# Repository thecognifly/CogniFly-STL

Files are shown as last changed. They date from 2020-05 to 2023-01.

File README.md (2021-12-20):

# CogniFly-STL
3D files (STL) for printing and assembling current and past versions of CogniFly

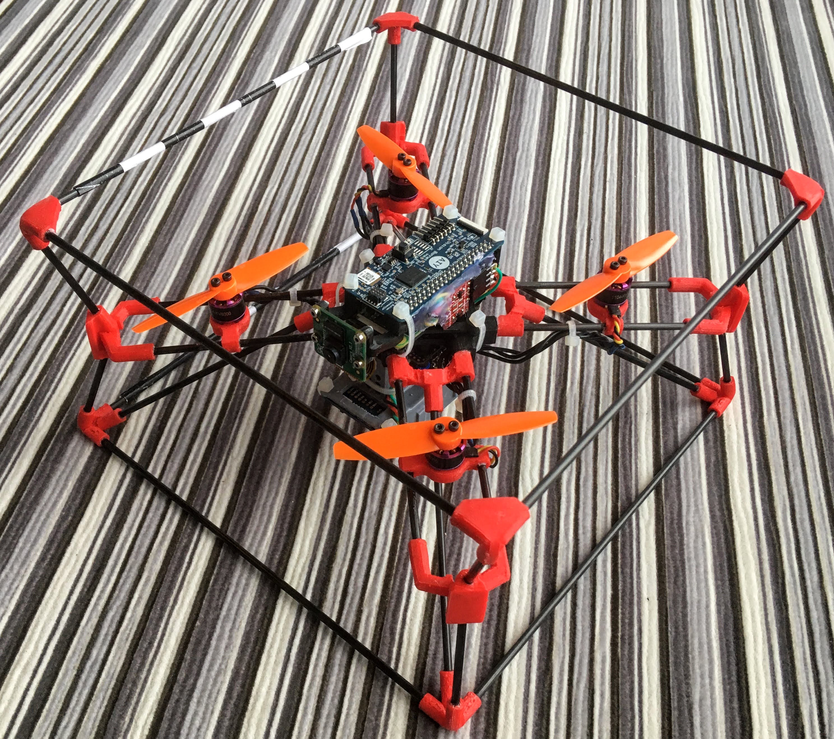
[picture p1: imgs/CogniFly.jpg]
CogniFly


Fold as you assemble

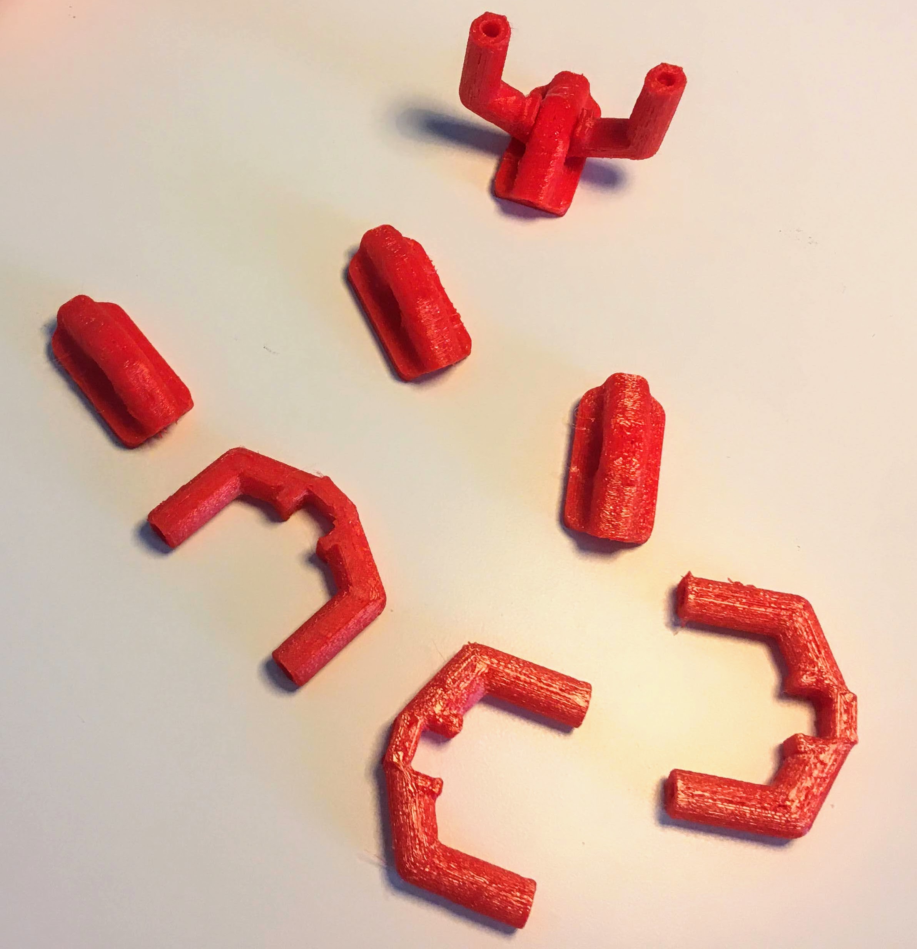
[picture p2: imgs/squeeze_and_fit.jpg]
Squeeze and fit


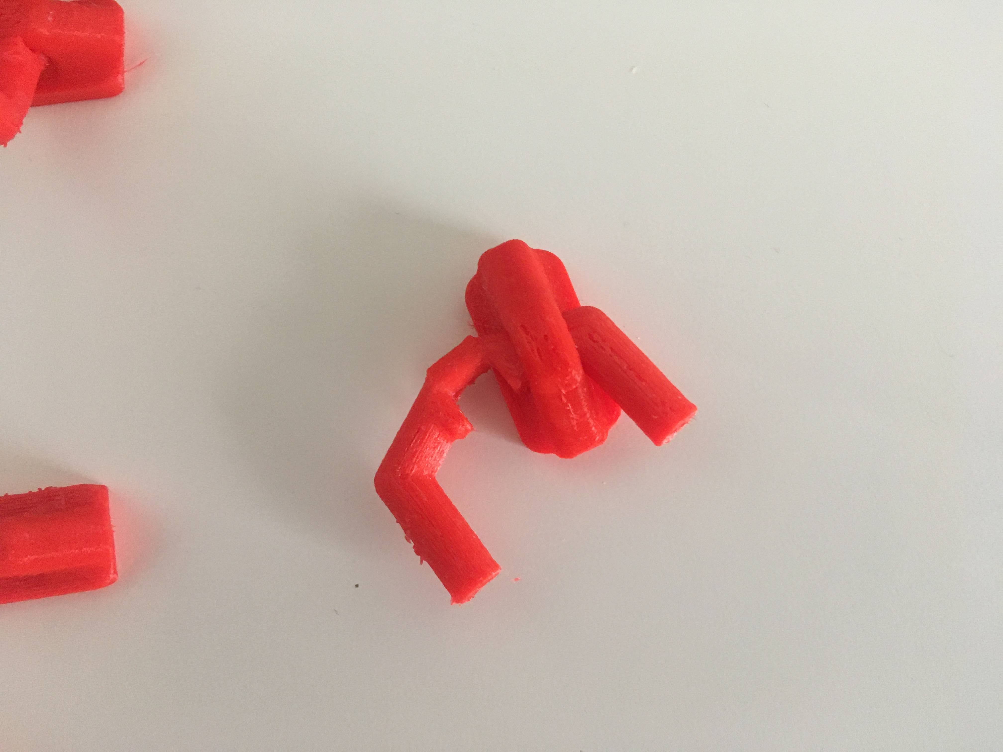
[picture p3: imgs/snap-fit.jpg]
Squeeze and fit 2

It's a very snug fit! You need to squeeze the round tube-like side, but without damaging it. Probably the hardest part to assemble.

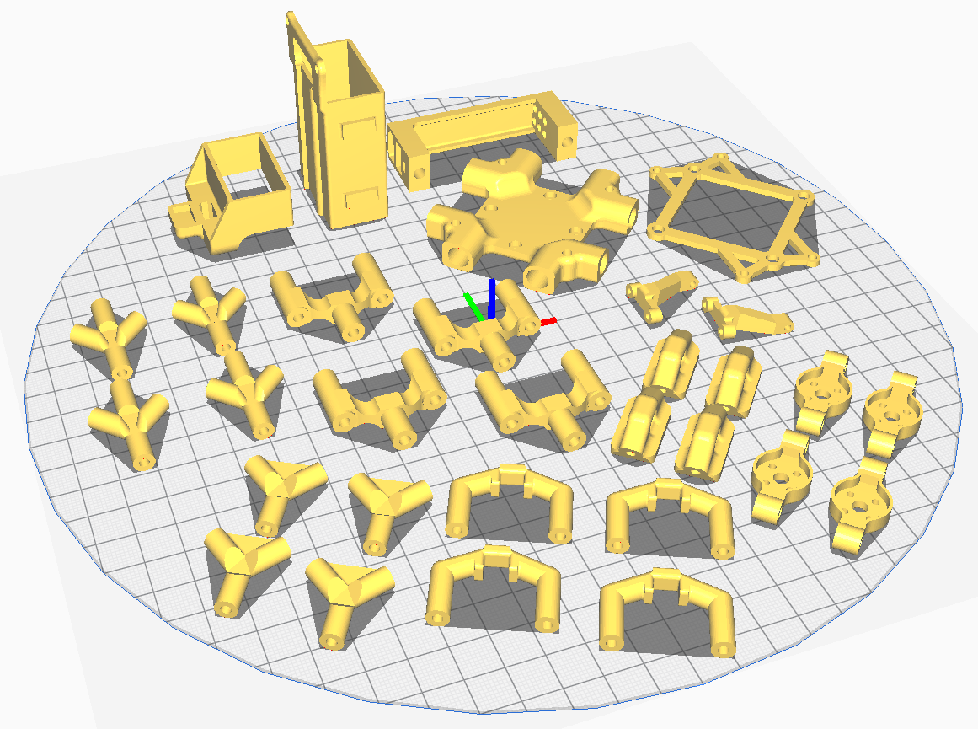
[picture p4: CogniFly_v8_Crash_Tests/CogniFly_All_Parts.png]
All parts together as they should be printed

The only part that needs support to be printed is the [Battery_holder_magnetic_lid.stl](CogniFly_v8_Crash_Tests/Battery_holder_magnetic_lid.stl). Depending on your printer, settings, fillament, etc. some holes will change the internal diameter and they may be too loose. In this case, you will need to glue the struts (carbon fiber or bamboo skewers) or, instead of absorbing the impact, the frame will just fall apart and almost no impact energy will be absorbed by the flexible parts. If you get a nice snug-fit between the struts and the TPU parts, you will not need to glue them together. In the case of bamboo, because they break much more easily than carbon fiber (never managed to break any!), if you glue them it will be annoying to replace.

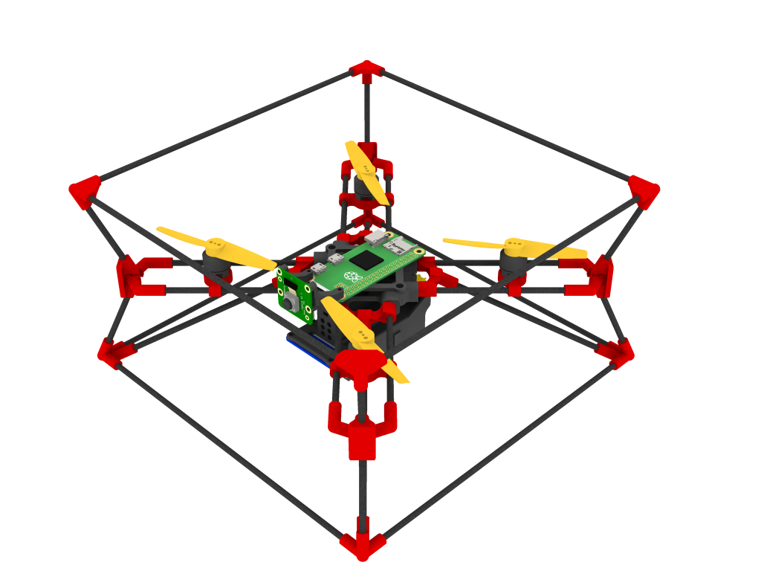
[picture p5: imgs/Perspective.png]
Render

All the parts in red are made of flexible TPU 95A. 

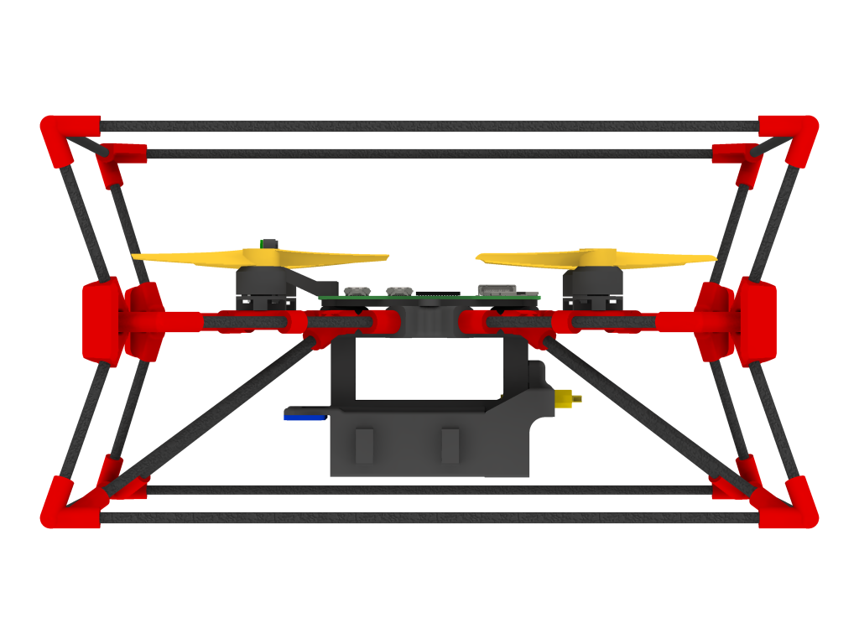
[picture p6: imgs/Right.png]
FC and ESC

Flight controller and ESC (4-in-1) are mounted between the battery and the central part of the frame (the empty space seeing above). The central was designed with 20x20mm mounting holes. The motors shown in the photograph at the top are 1104 ones and the holes are for M2, but be careful with the length of your screws so you don't destroy the motor windings!

## Bill of Materials (BOM)
### Brushless Motors and Propellers
- (4x) 1104 6000KV (use with 3025 2 blades propeller, used in our paper)  
**or**   
- (4x) 1106 3800KV (use with 4025 2 blades propeller, and it will need a bigger frame / longer struts or the [experimental motor bases](https://github.com/thecognifly/CogniFly-STL/blob/master/CogniFly_v8_Crash_Tests/MotorBase_Shorter_Taller.stl) to avoid hitting the RPI or AIY Bonnet)
### 3D Printing Filament
- TPU 95A for flexible parts
- PLA or ABS for the rigid ones
### Struts
- 3mm diam. carbon fibre rods or BBQ bamboo skewers with these approximate lengths: 8x 195mm (*"external cage"*), 8x 97mm (arms) and 4x 72mm (legs).
### Flight Controller (20x20mm mounting holes)
- (1x) Holybro Kakute F7 Mini V2 (used in our paper) or Heli-Nation Talon F7 Fusion
### 4 in 1 ESC (20x20mm mounting holes)
- (1x) Anyone that can deliver around 15A or 20A per motor to be safe (Spedix IS35 35A used in our paper)
### Firmware
- [Our INav fork with targets: KAKUTEF7 or CLRACINGF7](https://github.com/thecognifly/inav/tree/CogniFly)
- The standard INav should also work, but you will need to check if your flight controller is supported. BetaFlight will work, but it doesn't offer position hold.
### Battery
- LiPo Battery 650mAh 11.1V 75C 3S (TATTU used in our paper)
### Single-Board Computer
- [Raspberry Pi Zero W](https://www.raspberrypi.org/products/raspberry-pi-zero-w/)
### Camera
- [Raspberry Camera V2](https://www.raspberrypi.org/products/camera-module-v2/)
### Optical Flow and Time-of-Flight sensor
- [Matek Optical Flow and Lidar sensor](http://www.mateksys.com/?portfolio=3901-l0x)
### Neural Network Accelerator
- [Google AIY Vision Kit](https://aiyprojects.withgoogle.com/vision) (the Raspberry Pi Zero W + Camera are included). You don't really need it unless you want to run some neural network models. You can try the [Google Coral Edge TPU USB](https://github.com/ricardodeazambuja/libedgetpu-rpi0/releases/tag/rpi0_tflite_edgetpu) with [an adapter](https://shop.pimoroni.com/products/usb-to-microusb-otg-converter-shim) as well.
### Extras
- (1x) XT30 connector + cable to solder it to the ESC
- Cable zip ties (approx. 2mm wide)
- M2 screws / nuts / rubber rings to mount the ESC and FC (they usually come with the FC).
- Screws for mounting the motors and propellers (check the motor's manual to avoid damaging the motor with screws that are too long!)

## Caveats
1. The connection between one of the RPI Zero UARTs ([it has two](https://www.raspberrypi.org/documentation/configuration/uart.md)) and the flight controller may suffer from external interference, so twist it, try to use the shortest length, and keep it away from other cables (specially high current ones). For the same reason, some of the unused [pins from the AIY Vision Bonnet](https://pinout.xyz/pinout/aiy_vision_bonnet) were trimmed down to avoid problems with interference.
2. If you use super glue to assemble the bamboo version, it will be very hard to remove the bamboo sticks from the flexible 3D printed parts if the bamboo breaks.
3. The way parts are placed on the 3D printer bed is very important when using FDM printers because they will dramatically change the way the part behaves (weaker in some directions, layer adhesion, etc). Therefore, try to follow the suggested directions.
4. Carbon fiber needs to be cut using water / wet tissue to avoid problems with the fine dust generated, but even like that it's a serious health hazard. If you are not sure, start with the bamboo version. **Don't forget to wear protective equipment!**
5. We suggest initially building the frame using BBQ bamboo skewers (no glue!) so you will have the perfect template for cutting the carbon fibre rods later. The frame can be made bigger or smaller up to a certain scale just by choosing the correct lengths for the struts.

## Finally, this is a collision *resilient* design, but it has its physical limits as everything else in life. It will absorb a lot of energy even in the case where it flex so much that you manage to hit the internal electronics agains the obstacle, but in this case it may damage something that is fragile. We used poly carbonate propellers and they lasted quite a few crashes before becoming too damaged for flying :)

**For more details, check [thecognifly.github.io](https://thecognifly.github.io/).**

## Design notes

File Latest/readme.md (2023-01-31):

# Building Instructions (Version 2)

The Cognifly is a sub-250g drone with easy manufacturing, allowing
customization and autonomous flight. It has an optical flow and lidar,
allowing position and altitude hold, and a Raspberry Pi Zero W, allowing
wireless control and data processing. A Pi camera linked to the
Raspberry pi allows image processing to do an autonomous flight. The
flight controller is working with INAV, which allows an easy
configuration of the drone.

The frame is built with wood sticks and resists to impact while flying.
Another configuration is possible with carbon fiber, but it is more
expensive and heavier. The bamboo version of CogniFly weighs 237g (and, depending on the materials used, from 246 to 255g if you swap bamboo for carbon fibre rods in THIS version). It uses a LiPo battery 2S (7,4V) with a
2000mAh capacity, leading to a 17-minute flight time. (The test has been
made in one long flight, from 8,4V to 6,6V, in the position hold mode).

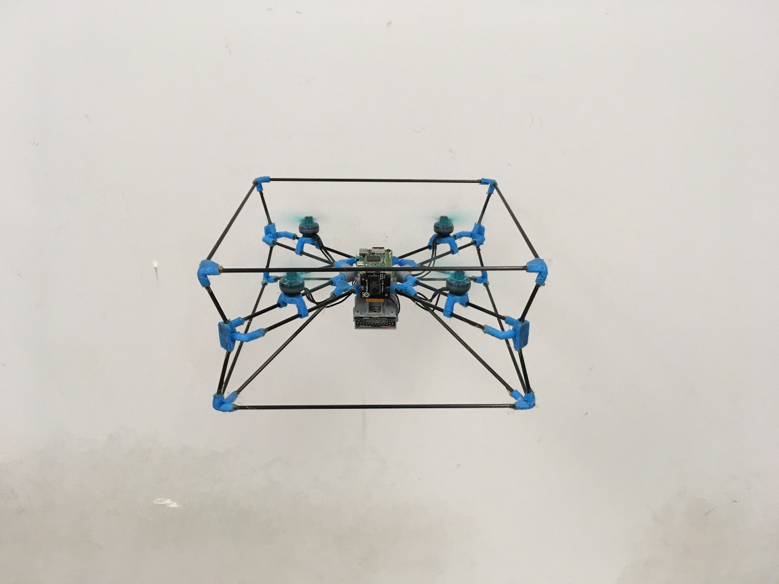
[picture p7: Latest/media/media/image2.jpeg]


## Table of Contents
1. [Bill of Materials](readme.md#bill-of-materials)
    * [Table 1: Description of the hardware for one drone](readme.md#table-1-description-of-the-hardware-for-one-drone)
    * [Table 2: Bill of Materials using a Raspberry Pi Zero](readme.md#table-2-bill-of-materials-using-a-raspberry-pi-zero)
    * [Table 3: Bill of Materials using a Google AIY Vision Kit](readme.md#table-3-bill-of-materials-using-a-google-aiy-vision-kit)
    * [Table 4: Bill of Materials using a Coral board](readme.md#table-4-bill-of-materials-using-a-coral-board)
2. [Building the drone](readme.md#building-the-drone)
    * [Frame](readme.md#frame)
    * [Electronics](readme.md#electronics)
    * [Putting everything together](readme.md#putting-everything-together)
3. [Software setup](readme.md#software-setup)
    * [INAV](readme.md#inav)
    * [Raspberry Pi Zero W](readme.md#raspberry-pi-zero-w)
4. [Troubleshooting](readme.md#troubleshooting)
    * [Wifi not working](readme.md#wifi-not-working)
    * [ssh not available](readme.md#ssh-not-available)
    * [Flashing the FC](readme.md#flashing-the-fc)
5. [Acknowledgements](readme.md#acknowledgements)

## Bill of Materials

To build this drone, some tools will be needed and not included in the
following list: a 3D printer (ideally two so you can print continuously
the TPU parts and the PLA parts for more than 1 drone), a soldering iron
with tin (and flux), a hot glue gun with glue, and a screwdriver for M2
screws, wire strippers, pliers…

### *Table 1: Description of the hardware for one drone*

<table>
<thead>
<tr class="header">
<th>Part Number</th>
<th>Item</th>
<th>Description</th>
<th>Quantity</th>
</tr>
</thead>
<tbody>
<tr class="odd">
<td>CF01-CF04</td>
<td><p>Wood stick</p>
<p><em>Or carbon fibre rods</em></p></td>
<td><p>Frame</p>
<p>Diameter: 3mm; Length : &gt;25cm</p></td>
<td>20 sticks</td>
</tr>
<tr class="even">
<td>CF05-CF10</td>
<td>TPU95a filament</td>
<td><p>Frame (Joints)</p>
<p>TPU95a filament; flexible plastic parts</p></td>
<td>34g</td>
</tr>
<tr class="odd">
<td>CF11-CF17</td>
<td>PLA filament</td>
<td><p>Structure</p>
<p>PLA filament; Hard plastic parts</p></td>
<td>24g</td>
</tr>
<tr class="even">
<td><p>CF18A</p>
<p>CF18B</p></td>
<td>Motor XING2 1404 3000KV</td>
<td><p>Motor XING2 1404<br />
3000KV; 10,1g</p>
<p>(7mm screws included used for propellers, Raspberry Pi, Camera, and optical flow attachment)</p></td>
<td><p>4</p>
<p>(18)</p></td>
</tr>
<tr class="odd">
<td>CF19</td>
<td>Screw spacer</td>
<td>M2/M3 Rubber Damping Ball (for raspberry pi and Optical flow)</td>
<td>4</td>
</tr>
<tr class="even">
<td><p>CF20A</p>
<p>CF20B</p></td>
<td>FC – ESC JHEMCU GHF420 35A</td>
<td><p>20x20mm Jhemcu GHF420AIO F4 OSD Flight Controller w/ 5V 9V BEC Output &amp; Built-in 35A BL_S 4In1 Brushless ESC</p>
<p>(4 Rubber Damping Balls included used for FC attachment)</p></td>
<td><p>1</p>
<p>(4)</p></td>
</tr>
<tr class="odd">
<td>CF21-CF22</td>
<td>Propellers 4024</td>
<td>Gemfan Hurricane 4024 2 Blades</td>
<td>2CW and 2CCW</td>
</tr>
<tr class="even">
<td>CF23</td>
<td>Matek Optical Flow and Lidar</td>
<td>Matek Optical Flow &amp; Lidar Sensor - 3901-L0X</td>
<td>1</td>
</tr>
<tr class="odd">
<td>CF24</td>
<td>Raspberry Pi Zero W</td>
<td>Raspberry Pi Zero W (Wireless)</td>
<td>1</td>
</tr>
<tr class="even">
<td>CF25</td>
<td>Pi camera</td>
<td>Raspberry Pi Camera V2 - 8MP</td>
<td>1</td>
</tr>
<tr class="odd">
<td>CF26</td>
<td>Mini camera cable</td>
<td>Raspberry Pi Zero Mini Camera Cable - 38mm</td>
<td>1</td>
</tr>
<tr class="even">
<td>CF27</td>
<td>Deans connector</td>
<td>Male Deans connector</td>
<td>1</td>
</tr>
<tr class="odd">
<td>CF28</td>
<td>SD card</td>
<td>Micro SD card &gt; 16Go</td>
<td>1</td>
</tr>
<tr class="even">
<td>CF29</td>
<td>Lipo 2S 2000mAh</td>
<td>Hosim Battery 9125; 2000 mAh LiPo Battery; 7,4V 25C</td>
<td>1 or more</td>
</tr>
<tr class="odd">
<td>CF30</td>
<td>M2 Screw 4mm</td>
<td>M2 Screw 4mm</td>
<td>16</td>
</tr>
<tr class="even">
<td>CF31</td>
<td>M2 Screw 16mm</td>
<td>M2 Screw 16mm</td>
<td>6</td>
</tr>
<tr class="odd">
<td>CF32</td>
<td>Wire 28/32 AWG</td>
<td>4 Wires 28/32 AWG (4 colors)</td>
<td>2X15cm</td>
</tr>
<tr class="even">
<td><em>CF33</em></td>
<td>Vision Bonnet</td>
<td>Google AIY Vision Bonnet</td>
<td>1 (<em>optional</em>)</td>
</tr>
</tbody>
</table>

The Vision bonnet is optional but allows to compute more data faster,
which can be useful for image processing.

The following tables (2 to 4) presents some website where to order the
material. Table 2 uses the Raspberry Pi Zero without Google vision kit;
table 3 uses the Raspberry Pi Zero with Google vision kit; table 4 uses
the Mini Coral board instead of the Raspberry Pi.

### *Table 2: Bill of Materials using a Raspberry Pi Zero*

<table>
<thead>
<tr class="header">
<th>Item</th>
<th>Link Canada 2021</th>
<th>Quantity</th>
<th>Drone quantity</th>
<th>Price (CAD)</th>
<th>Price for one drone</th>
<th>Price for 5 drones</th>
<th>Price for 10 drones</th>
</tr>
</thead>
<tbody>
<tr class="odd">
<td>Wood stick</td>
<td><a href="https://www.amazon.ca/-/fr/Chef-Craft-brochettes-fines-bambou/dp/B075YFB1SZ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"><span class="underline">Amazon</span></a><br />
grocery store</td>
<td>1</td>
<td>6</td>
<td>8,67</td>
<td>8,67</td>
<td>8,67</td>
<td>17,34</td>
</tr>
<tr class="even">
<td>TPU95a filament</td>
<td><a href="https://www.amazon.ca/Polymaker-PolyFlex-Flexible-Filament-Dimensional/dp/B083XFT675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"><span class="underline">Amazon</span></a></td>
<td>1</td>
<td>15+</td>
<td>39,99</td>
<td>39,99</td>
<td>39,99</td>
<td>39,99</td>
</tr>
<tr class="odd">
<td>PLA filament</td>
<td><a href="https://www.amazon.ca/construction-pr%C3%A9cision-dimensionnelle-compatible-imprimantes/dp/B07PGZNM34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"><span class="underline">Amazon</span></a></td>
<td>1</td>
<td>15+</td>
<td>28,99</td>
<td>28,99</td>
<td>28,99</td>
<td>28,99</td>
</tr>
<tr class="even">
<td>Motor XING2 1404 3000KV</td>
<td><a href="https://shop.iflight-rc.com/motors-cat88/xing2-1404-toothpick-ultralight-build-unibell-pro1482"><span class="underline">Iflight</span></a><br />
<a href="https://www.banggood.com/IFlight-XING2-1404-3000KV-3800KV-4600KV-2-4S-Brushless-Motor-for-Toothpick-RC-Drone-FPV-Racing-p-1817793.html?ID=517763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"><span class="underline">Banggood</span></a></td>
<td>4</td>
<td>1</td>
<td>20,50<br />
(26,95)</td>
<td>20,50</td>
<td>102,50</td>
<td>205,00</td>
</tr>
<tr class="odd">
<td>Screw spacer</td>
<td><p><a href="https://shop.iflight-rc.com/m2-m3-rubber-damping-ball-for-f4-f7-32k-flight-control-40pcs-pro294?search=rubber"><span class="underline">iflight</span></a></p>
<p><a href="https://www.banggood.com/20-PCS-SupraRC-M2x4-M2-Anti-vibration-Standoff-Rubber-Damping-Ball-for-F7BT-Flight-Controller-ESC-RC-Drone-FPV-Racing-p-1716028.html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"><span class="underline">Banggood</span></a></p></td>
<td>1</td>
<td>10<br />
5</td>
<td>8,96<br />
(10,26)</td>
<td>8,96</td>
<td>8,96</td>
<td>8,96</td>
</tr>
<tr class="even">
<td>FC – ESC JHEMCU GHF420 35A</td>
<td><p><a href="https://www.cyclonefpv.com/products/jhemcu-ghf420-aio-20x20-fc-20a-and-30a-options?variant=32949263695915"><span class="underline">cycloneFPV</span></a></p>
<p><a href="https://rotorvillage.ca/jhemcu-ghf420-f4-35a-aio-flight-controller/"><span class="underline">RotorVillage</span></a></p>
<p><a href="https://www.banggood.com/20x20mm-Jhemcu-GHF420AIO-F4-OSD-Flight-Controller-w-or-5V-9V-BEC-Output-and-Built-in-35A-BL_S-4In1-Brushless-ESC-Support-DJI-Air-Unit-for-RC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"><span class="underline">Banggood</span></a></p></td>
<td>1</td>
<td>1</td>
<td><p>76,92</p>
<p>(83,99)</p>
<p>(92,42)</p></td>
<td>76,92</td>
<td>384,6</td>
<td>769,20</td>
</tr>
<tr class="odd">
<td>Propellers 4024</td>
<td><p><a href="https://www.cyclonefpv.com/collections/4-props/products/gemfan-hurricane-4024-2-blade-1408-1506-motor-props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"><span class="underline">CycloneFPV</span></a></p>
<p><a href="https://rotorvillage.ca/gemfan-4024-hurricane-prop/"><span class="underline">RotorVillage</span></a></p>
<p><a href="https://www.banggood.com/4-Pairs-Gemfan-Hurricane-4024-2-blade-4-Inch-PC-Propeller-for-1408-1506-Brushless-Motor-RC-Drone-FPV-Racing-p-1657418.html?ID=3237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"><span class="underline">Banggood</span></a></p></td>
<td>1</td>
<td>2</td>
<td><p>4,47</p>
<p>(5,49)</p>
<p>(10,26)</p></td>
<td>4,47</td>
<td>13,41</td>
<td>22,35</td>
</tr>
<tr class="even">
<td>Matek Optical Flow and Lidar</td>
<td><p><a href="https://www.getfpv.com/matek-optical-flow-lidar-sensor-3901-l0x.html"><span class="underline">GetFPV</span></a></p>
<p><a href="https://rotorvillage.ca/Matek-3901-L0X-Optical-Flow-Lidar-Sensor/"><span class="underline">RotorVillage</span></a></p>
<p><a href="https://www.amazon.ca/-/fr/Systems-3901-L0X-capteur-optique-quadrirotor/dp/B082LYQGDD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"><span class="underline">Amazon</span></a><br />
<a href="https://can.grandado.com/products/style-matek-system-optical-flow-lidar-sensor-3901-l0x-module-support-inav-for-rc-drone-fpv-racing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"><span class="underline">Grandado</span></a></p></td>
<td>1</td>
<td>1</td>
<td><p>38,46</p>
<p>(38,99)</p>
<p>(96,22)</p>
<p>(77,09)</p></td>
<td>38,46</td>
<td>192,30</td>
<td>384,60</td>
</tr>
<tr class="odd">
<td>Raspberry Pi Zero W</td>
<td><p><a href="https://www.canakit.com/raspberry-pi-zero-wireless.html?defpid=4328"><span class="underline">Canakit</span></a></p>
<p><a href="https://www.amazon.ca/-/fr/Zero-W-Raspberry-Pi-W/dp/B06XFZC3BX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"><span class="underline">Amazon</span></a></p>
<p><a href="https://www.pishop.ca/product/raspberry-pi-zero-w/"><span class="underline">Pishop</span></a></p>
<p><a href="https://www.banggood.com/Raspberry-Pi-Zero-W-Board-Version-with-1GHz-CPU-512MB-LPDDR2-SDRAM-bluetooth-4_1-p-1774468.html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"><span class="underline">Banggood</span></a></p></td>
<td>1</td>
<td>1</td>
<td><p>29,78</p>
<p>(43,99)</p>
<p>(14,24)</p>
<p>(55,19)</p></td>
<td>29,78</td>
<td>148,90</td>
<td>297,80</td>
</tr>
<tr class="even">
<td>Pi camera</td>
<td><a href="https://www.pishop.ca/product/raspberry-pi-noir-camera-module-v2-8mp/"><span class="underline">Pishop</span></a></td>
<td>1</td>
<td>1</td>
<td>35,95</td>
<td>35,95</td>
<td>179,75</td>
<td>359,50</td>
</tr>
<tr class="odd">
<td>Mini camera cable</td>
<td><a href="https://www.pishop.ca/product/raspberry-pi-zero-mini-camera-cable-38mm/"><span class="underline">Pishop</span></a></td>
<td>1</td>
<td>1</td>
<td>2,95</td>
<td>2,95</td>
<td>14,75</td>
<td>29,50</td>
</tr>
<tr class="even">
<td>Deans connector</td>
<td><a href="https://www.amazon.ca/-/fr/UEETEK-paires-connecteurs-ultra-batterie/dp/B077TXMTJZ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"><span class="underline">Amazon</span></a><br />
<a href="https://www.amazon.ca/paires-connecteurs-femelles-silicone-batterie/dp/B07WHPD4KD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"><span class="underline">Amazon</span></a></td>
<td>1</td>
<td><p>10</p>
<p>5</p></td>
<td><p>11,99</p>
<p>(12,99)</p></td>
<td>11,99</td>
<td>11,99</td>
<td>11,99</td>
</tr>
<tr class="odd">
<td>SD card</td>
<td><p><a href="https://www.amazon.ca/Gigastone-cartes-surveillance-daction-professionnelle/dp/B07XB42B99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"><span class="underline">Amazon</span></a></p>
<p><a href="https://www.amazon.ca/-/fr/SanDisk-SDSQUAR-064G-GN6MA-m%C3%A9moire-microSDXC-adaptateur/dp/B073JYVKNX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"><span class="underline">Amazon</span></a></p></td>
<td><p>1</p>
<p>1</p></td>
<td><p>5</p>
<p>1</p></td>
<td><p>59,98</p>
<p>(15,39)</p></td>
<td>15,39</td>
<td>59,98</td>
<td>119,96</td>
</tr>
<tr class="even">
<td>Lipo 2S 2000mAh</td>
<td><a href="https://www.amazon.ca/-/fr/Hosim-Batterie-rechargeable-25-DJ02-%C3%89chelle/dp/B07SW2K4P4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"><span class="underline">Amazon</span></a></td>
<td>2</td>
<td>1</td>
<td>25,98</td>
<td>51,96</td>
<td>259,80</td>
<td>519,60</td>
</tr>
<tr class="odd">
<td>M2 Screw 4mm</td>
<td><p><a href="https://www.cyclonefpv.com/products/m2-drone-screws-socket-head-cap-9-sizes-100-count-steel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"><span class="underline">CycloneFPV</span></a></p>
<p><a href="https://rotorvillage.ca/m2-x-5mm-black-steel-button-head-screw-8pk/"><span class="underline">RotorVillage</span></a><br />
<a href="https://www.amazon.ca/-/fr/XunLiu-molet%C3%A9es-hexagonale-alliage-dacier/dp/B07CHM7ZQK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"><span class="underline">Amazon</span></a></p></td>
<td><p>2</p>
<p>2</p>
<p>1</p></td>
<td><p>1</p>
<p>1</p>
<p>6</p></td>
<td><p>1,27</p>
<p>(2,49)</p>
<p>(46,06)</p></td>
<td>2,54</td>
<td>12,70</td>
<td>25,40</td>
</tr>
<tr class="even">
<td>M2 Screw 16mm</td>
<td><p><a href="https://www.cyclonefpv.com/products/m2-drone-screws-socket-head-cap-9-sizes-100-count-steel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"><span class="underline">CycloneFPV</span></a></p>
<p><a href="https://rotorvillage.ca/m2-x-16mm-black-steel-button-head-screw-8pk/"><span class="underline">RotorVillage</span></a></p>
<p><a href="https://www.amazon.ca/-/fr/XunLiu-molet%C3%A9es-hexagonale-alliage-dacier/dp/B07CHGZT5K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"><span class="underline">Amazon</span></a></p></td>
<td><p>1</p>
<p>1</p></td>
<td><p>1</p>
<p>16</p></td>
<td><p>1,27</p>
<p>(2,79)</p>
<p>(11,79)</p></td>
<td>1,27</td>
<td>6,35</td>
<td>12,70</td>
</tr>
<tr class="odd">
<td>Wire 28/32 AWG</td>
<td><a href="https://www.amazon.ca/1007-Bo%C3%AEte-solide-avec-%C3%A9lectriques/dp/B073RDGTPB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"><span class="underline">Amazon</span></a></td>
<td>1</td>
<td>15+</td>
<td>19,88</td>
<td>19,88</td>
<td>19,88</td>
<td>19,88</td>
</tr>
<tr class="even">
<td>Electrical tape</td>
<td><a href="https://www.amazon.ca/-/fr/Temflex-TEMFLEX-3-4X60-adh%C3%A9sif-%C3%A9lectrique/dp/B003DXV9HY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"><span class="underline">Amazon</span></a></td>
<td>1</td>
<td>15+</td>
<td>1,24</td>
<td>1,24</td>
<td>1,24</td>
<td>1,24</td>
</tr>
<tr class="odd">
<td>Hot glue</td>
<td><a href="https://www.amazon.ca/-/fr/Adtech-W220-34ZIP30-b%C3%A2tons-colle-chaude/dp/B00009RUCS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"><span class="underline">Amazon</span></a></td>
<td>1</td>
<td>15+</td>
<td>7,99</td>
<td>7,99</td>
<td>7,99</td>
<td>7,99</td>
</tr>
<tr class="even">
<td colspan="5">Total</td>
<td>407,9</td>
<td>1502,75</td>
<td>2881,99</td>
</tr>
<tr class="odd">
<td colspan="5">Unit total</td>
<td>407,9</td>
<td>300,55</td>
<td>288,199</td>
</tr>
</tbody>
</table>

### *Table 3: Bill of Materials using a Google AIY Vision Kit*

<table>
<thead>
<tr class="header">
<th>Item</th>
<th>Link Canada 2021</th>
<th>Quantity</th>
<th>Drone quantity</th>
<th>Price (CAD)</th>
<th>Price for one drone</th>
<th>Price for 5 drones</th>
<th>Price for 10 drones</th>
</tr>
</thead>
<tbody>
<tr class="odd">
<td>Wood stick</td>
<td><a href="https://www.amazon.ca/-/fr/Chef-Craft-brochettes-fines-bambou/dp/B075YFB1SZ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"><span class="underline">Amazon</span></a><br />
grocery store</td>
<td>1</td>
<td>6</td>
<td>8,67</td>
<td>8,67</td>
<td>8,67</td>
<td>17,34</td>
</tr>
<tr class="even">
<td>TPU95a filament</td>
<td><a href="https://www.amazon.ca/Polymaker-PolyFlex-Flexible-Filament-Dimensional/dp/B083XFT675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"><span class="underline">Amazon</span></a></td>
<td>1</td>
<td>15+</td>
<td>39,99</td>
<td>39,99</td>
<td>39,99</td>
<td>39,99</td>
</tr>
<tr class="odd">
<td>PLA filament</td>
<td><a href="https://www.amazon.ca/construction-pr%C3%A9cision-dimensionnelle-compatible-imprimantes/dp/B07PGZNM34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"><span class="underline">Amazon</span></a></td>
<td>1</td>
<td>15+</td>
<td>28,99</td>
<td>28,99</td>
<td>28,99</td>
<td>28,99</td>
</tr>
<tr class="even">
<td>Motor XING2 1404 3000KV</td>
<td><a href="https://shop.iflight-rc.com/motors-cat88/xing2-1404-toothpick-ultralight-build-unibell-pro1482"><span class="underline">Iflight</span></a><br />
<a href="https://www.banggood.com/IFlight-XING2-1404-3000KV-3800KV-4600KV-2-4S-Brushless-Motor-for-Toothpick-RC-Drone-FPV-Racing-p-1817793.html?ID=517763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"><span class="underline">Banggood</span></a></td>
<td>4</td>
<td>1</td>
<td>20,50<br />
(26,95)</td>
<td>20,50</td>
<td>102,50</td>
<td>205,00</td>
</tr>
<tr class="odd">
<td>Screw spacer</td>
<td><p><a href="https://shop.iflight-rc.com/m2-m3-rubber-damping-ball-for-f4-f7-32k-flight-control-40pcs-pro294?search=rubber"><span class="underline">iflight</span></a></p>
<p><a href="https://www.banggood.com/20-PCS-SupraRC-M2x4-M2-Anti-vibration-Standoff-Rubber-Damping-Ball-for-F7BT-Flight-Controller-ESC-RC-Drone-FPV-Racing-p-1716028.html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"><span class="underline">Banggood</span></a></p></td>
<td>1</td>
<td>10<br />
5</td>
<td>8,96<br />
(10,26)</td>
<td>8,96</td>
<td>8,96</td>
<td>8,96</td>
</tr>
<tr class="even">
<td>FC – ESC JHEMCU GHF420 35A</td>
<td><p><a href="https://www.cyclonefpv.com/products/jhemcu-ghf420-aio-20x20-fc-20a-and-30a-options?variant=32949263695915"><span class="underline">cycloneFPV</span></a></p>
<p><a href="https://rotorvillage.ca/jhemcu-ghf420-f4-35a-aio-flight-controller/"><span class="underline">RotorVillage</span></a></p>
<p><a href="https://www.banggood.com/20x20mm-Jhemcu-GHF420AIO-F4-OSD-Flight-Controller-w-or-5V-9V-BEC-Output-and-Built-in-35A-BL_S-4In1-Brushless-ESC-Support-DJI-Air-Unit-for-RC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"><span class="underline">Banggood</span></a></p></td>
<td>1</td>
<td>1</td>
<td><p>76,92</p>
<p>(83,99)</p>
<p>(92,42)</p></td>
<td>76,92</td>
<td>384,6</td>
<td>769,20</td>
</tr>
<tr class="odd">
<td>Propellers 4024</td>
<td><p><a href="https://www.cyclonefpv.com/collections/4-props/products/gemfan-hurricane-4024-2-blade-1408-1506-motor-props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"><span class="underline">CycloneFPV</span></a></p>
<p><a href="https://rotorvillage.ca/gemfan-4024-hurricane-prop/"><span class="underline">RotorVillage</span></a></p>
<p><a href="https://www.banggood.com/4-Pairs-Gemfan-Hurricane-4024-2-blade-4-Inch-PC-Propeller-for-1408-1506-Brushless-Motor-RC-Drone-FPV-Racing-p-1657418.html?ID=3237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"><span class="underline">Banggood</span></a></p></td>
<td>1</td>
<td>2</td>
<td><p>4,47</p>
<p>(5,49)</p>
<p>(10,26)</p></td>
<td>4,47</td>
<td>13,41</td>
<td>22,35</td>
</tr>
<tr class="even">
<td>Matek Optical Flow and Lidar</td>
<td><p><a href="https://www.getfpv.com/matek-optical-flow-lidar-sensor-3901-l0x.html"><span class="underline">GetFPV</span></a></p>
<p><a href="https://rotorvillage.ca/Matek-3901-L0X-Optical-Flow-Lidar-Sensor/"><span class="underline">RotorVillage</span></a></p>
<p><a href="https://www.amazon.ca/-/fr/Systems-3901-L0X-capteur-optique-quadrirotor/dp/B082LYQGDD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"><span class="underline">Amazon</span></a><br />
<a href="https://can.grandado.com/products/style-matek-system-optical-flow-lidar-sensor-3901-l0x-module-support-inav-for-rc-drone-fpv-racing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"><span class="underline">Grandado</span></a></p></td>
<td>1</td>
<td>1</td>
<td><p>38,46</p>
<p>(38,99)</p>
<p>(96,22)</p>
<p>(77,09)</p></td>
<td>38,46</td>
<td>192,30</td>
<td>384,60</td>
</tr>
<tr class="odd">
<td>Google AIY Vision Kit</td>
<td><p><a href="https://store.gravitylink.com/global/product/vision-kit"><span class="underline">GravityLink</span></a></p>
<p><a href="https://www.adafruit.com/product/3780"><span class="underline">Adafruit</span></a></p></td>
<td>1</td>
<td>1</td>
<td><p>115,07</p>
<p>(128,14)</p></td>
<td>115,07</td>
<td>575,35</td>
<td>1150,70</td>
</tr>
<tr class="even">
<td>38mm Camera Cable</td>
<td><a href="https://www.pishop.us/product/raspberry-pi-zero-mini-camera-cable-38mm/"><span class="underline">PiShop</span></a></td>
<td>1</td>
<td>1</td>
<td>2,73</td>
<td>2,73</td>
<td>13,65</td>
<td>27,30</td>
</tr>
<tr class="odd">
<td>Deans connector</td>
<td><a href="https://www.amazon.ca/-/fr/UEETEK-paires-connecteurs-ultra-batterie/dp/B077TXMTJZ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"><span class="underline">Amazon</span></a><br />
<a href="https://www.amazon.ca/paires-connecteurs-femelles-silicone-batterie/dp/B07WHPD4KD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"><span class="underline">Amazon</span></a></td>
<td>1</td>
<td><p>10</p>
<p>5</p></td>
<td><p>11,99</p>
<p>(12,99)</p></td>
<td>11,99</td>
<td>11,99</td>
<td>11,99</td>
</tr>
<tr class="even">
<td>Lipo 2S 2000mAh</td>
<td><a href="https://www.amazon.ca/-/fr/Hosim-Batterie-rechargeable-25-DJ02-%C3%89chelle/dp/B07SW2K4P4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"><span class="underline">Amazon</span></a></td>
<td>2</td>
<td>1</td>
<td>25,98</td>
<td>51,96</td>
<td>259,80</td>
<td>519,60</td>
</tr>
<tr class="odd">
<td>M2 Screw 4mm</td>
<td><p><a href="https://www.cyclonefpv.com/products/m2-drone-screws-socket-head-cap-9-sizes-100-count-steel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"><span class="underline">CycloneFPV</span></a></p>
<p><a href="https://rotorvillage.ca/m2-x-5mm-black-steel-button-head-screw-8pk/"><span class="underline">RotorVillage</span></a><br />
<a href="https://www.amazon.ca/-/fr/XunLiu-molet%C3%A9es-hexagonale-alliage-dacier/dp/B07CHM7ZQK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"><span class="underline">Amazon</span></a></p></td>
<td><p>2</p>
<p>2</p>
<p>1</p></td>
<td><p>1</p>
<p>1</p>
<p>6</p></td>
<td><p>1,27</p>
<p>(2,49)</p>
<p>(46,06)</p></td>
<td>2,54</td>
<td>12,70</td>
<td>25,40</td>
</tr>
<tr class="even">
<td>M2 Screw 16mm</td>
<td><p><a href="https://www.cyclonefpv.com/products/m2-drone-screws-socket-head-cap-9-sizes-100-count-steel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"><span class="underline">CycloneFPV</span></a></p>
<p><a href="https://rotorvillage.ca/m2-x-16mm-black-steel-button-head-screw-8pk/"><span class="underline">RotorVillage</span></a></p>
<p><a href="https://www.amazon.ca/-/fr/XunLiu-molet%C3%A9es-hexagonale-alliage-dacier/dp/B07CHGZT5K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"><span class="underline">Amazon</span></a></p></td>
<td><p>1</p>
<p>1</p></td>
<td><p>1</p>
<p>16</p></td>
<td><p>1,27</p>
<p>(2,79)</p>
<p>(11,79)</p></td>
<td>1,27</td>
<td>6,35</td>
<td>12,70</td>
</tr>
<tr class="odd">
<td>Wire 28/32 AWG</td>
<td><a href="https://www.amazon.ca/1007-Bo%C3%AEte-solide-avec-%C3%A9lectriques/dp/B073RDGTPB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"><span class="underline">Amazon</span></a></td>
<td>1</td>
<td>15+</td>
<td>19,88</td>
<td>19,88</td>
<td>19,88</td>
<td>19,88</td>
</tr>
<tr class="even">
<td>Electrical tape</td>
<td><a href="https://www.amazon.ca/-/fr/Temflex-TEMFLEX-3-4X60-adh%C3%A9sif-%C3%A9lectrique/dp/B003DXV9HY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"><span class="underline">Amazon</span></a></td>
<td>1</td>
<td>15+</td>
<td>1,24</td>
<td>1,24</td>
<td>1,24</td>
<td>1,24</td>
</tr>
<tr class="odd">
<td>Hot glue</td>
<td><a href="https://www.amazon.ca/-/fr/Adtech-W220-34ZIP30-b%C3%A2tons-colle-chaude/dp/B00009RUCS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"><span class="underline">Amazon</span></a></td>
<td>1</td>
<td>15+</td>
<td>7,99</td>
<td>7,99</td>
<td>7,99</td>
<td>7,99</td>
</tr>
<tr class="even">
<td colspan="5">Total</td>
<td>441,63</td>
<td>1688.37</td>
<td>3253,23</td>
</tr>
<tr class="odd">
<td colspan="5">Unit total</td>
<td>441,63</td>
<td>337,67</td>
<td>325,32</td>
</tr>
</tbody>
</table>

If the vision kit from google is used, it already includes the Raspberry
Pi Zero, the Pi camera, the SD card, and the mini camera cable. The
vision bonnet can be useful for advanced image processing. Moreover, as
the Raspberry Pi Zero W can be difficult to order alone (only one per
order otherwise expensive), this choice can be a good solution.

### *Table 4: Bill of Materials using a Coral board*

<table>
<thead>
<tr class="header">
<th>Item</th>
<th>Link Canada 2021</th>
<th>Quantity</th>
<th>Drone quantity</th>
<th>Price (CAD)</th>
<th>Price for one drone</th>
<th>Price for 5 drones</th>
<th>Price for 10 drones</th>
</tr>
</thead>
<tbody>
<tr class="odd">
<td>Wood stick</td>
<td><a href="https://www.amazon.ca/-/fr/Chef-Craft-brochettes-fines-bambou/dp/B075YFB1SZ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"><span class="underline">Amazon</span></a><br />
grocery store</td>
<td>1</td>
<td>6</td>
<td>8,67</td>
<td>8,67</td>
<td>8,67</td>
<td>17,34</td>
</tr>
<tr class="even">
<td>TPU95a filament</td>
<td><a href="https://www.amazon.ca/Polymaker-PolyFlex-Flexible-Filament-Dimensional/dp/B083XFT675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"><span class="underline">Amazon</span></a></td>
<td>1</td>
<td>15+</td>
<td>39,99</td>
<td>39,99</td>
<td>39,99</td>
<td>39,99</td>
</tr>
<tr class="odd">
<td>PLA filament</td>
<td><a href="https://www.amazon.ca/construction-pr%C3%A9cision-dimensionnelle-compatible-imprimantes/dp/B07PGZNM34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"><span class="underline">Amazon</span></a></td>
<td>1</td>
<td>15+</td>
<td>28,99</td>
<td>28,99</td>
<td>28,99</td>
<td>28,99</td>
</tr>
<tr class="even">
<td>Motor XING2 1404 3000KV</td>
<td><a href="https://shop.iflight-rc.com/motors-cat88/xing2-1404-toothpick-ultralight-build-unibell-pro1482"><span class="underline">Iflight</span></a><br />
<a href="https://www.banggood.com/IFlight-XING2-1404-3000KV-3800KV-4600KV-2-4S-Brushless-Motor-for-Toothpick-RC-Drone-FPV-Racing-p-1817793.html?ID=517763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"><span class="underline">Banggood</span></a></td>
<td>4</td>
<td>1</td>
<td>20,50<br />
(26,95)</td>
<td>20,50</td>
<td>102,50</td>
<td>205,00</td>
</tr>
<tr class="odd">
<td>Screw spacer</td>
<td><p><a href="https://shop.iflight-rc.com/m2-m3-rubber-damping-ball-for-f4-f7-32k-flight-control-40pcs-pro294?search=rubber"><span class="underline">iflight</span></a></p>
<p><a href="https://www.banggood.com/20-PCS-SupraRC-M2x4-M2-Anti-vibration-Standoff-Rubber-Damping-Ball-for-F7BT-Flight-Controller-ESC-RC-Drone-FPV-Racing-p-1716028.html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"><span class="underline">Banggood</span></a></p></td>
<td>1</td>
<td>10<br />
5</td>
<td>8,96<br />
(10,26)</td>
<td>8,96</td>
<td>8,96</td>
<td>8,96</td>
</tr>
<tr class="even">
<td>FC – ESC JHEMCU GHF420 35A</td>
<td><p><a href="https://www.cyclonefpv.com/products/jhemcu-ghf420-aio-20x20-fc-20a-and-30a-options?variant=32949263695915"><span class="underline">cycloneFPV</span></a></p>
<p><a href="https://rotorvillage.ca/jhemcu-ghf420-f4-35a-aio-flight-controller/"><span class="underline">RotorVillage</span></a></p>
<p><a href="https://www.banggood.com/20x20mm-Jhemcu-GHF420AIO-F4-OSD-Flight-Controller-w-or-5V-9V-BEC-Output-and-Built-in-35A-BL_S-4In1-Brushless-ESC-Support-DJI-Air-Unit-for-RC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"><span class="underline">Banggood</span></a></p></td>
<td>1</td>
<td>1</td>
<td><p>76,92</p>
<p>(83,99)</p>
<p>(92,42)</p></td>
<td>76,92</td>
<td>384,6</td>
<td>769,20</td>
</tr>
<tr class="odd">
<td>Propellers 4024</td>
<td><p><a href="https://www.cyclonefpv.com/collections/4-props/products/gemfan-hurricane-4024-2-blade-1408-1506-motor-props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"><span class="underline">CycloneFPV</span></a></p>
<p><a href="https://rotorvillage.ca/gemfan-4024-hurricane-prop/"><span class="underline">RotorVillage</span></a></p>
<p><a href="https://www.banggood.com/4-Pairs-Gemfan-Hurricane-4024-2-blade-4-Inch-PC-Propeller-for-1408-1506-Brushless-Motor-RC-Drone-FPV-Racing-p-1657418.html?ID=3237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"><span class="underline">Banggood</span></a></p></td>
<td>1</td>
<td>2</td>
<td><p>4,47</p>
<p>(5,49)</p>
<p>(10,26)</p></td>
<td>4,47</td>
<td>13,41</td>
<td>22,35</td>
</tr>
<tr class="even">
<td>Matek Optical Flow and Lidar</td>
<td><p><a href="https://www.getfpv.com/matek-optical-flow-lidar-sensor-3901-l0x.html"><span class="underline">GetFPV</span></a></p>
<p><a href="https://rotorvillage.ca/Matek-3901-L0X-Optical-Flow-Lidar-Sensor/"><span class="underline">RotorVillage</span></a></p>
<p><a href="https://www.amazon.ca/-/fr/Systems-3901-L0X-capteur-optique-quadrirotor/dp/B082LYQGDD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"><span class="underline">Amazon</span></a><br />
<a href="https://can.grandado.com/products/style-matek-system-optical-flow-lidar-sensor-3901-l0x-module-support-inav-for-rc-drone-fpv-racing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"><span class="underline">Grandado</span></a></p></td>
<td>1</td>
<td>1</td>
<td><p>38,46</p>
<p>(38,99)</p>
<p>(96,22)</p>
<p>(77,09)</p></td>
<td>38,46</td>
<td>192,30</td>
<td>384,60</td>
</tr>
<tr class="odd">
<td>Coral Dev Board Mini</td>
<td><p><a href="https://www.seeedstudio.com/Coral-Dev-Board-Mini-p-4682.html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"><span class="underline">Seeed</span></a></p>
<p><a href="https://www.arrow.com/en/products/g650-03324-01/google-corporation"><span class="underline">Arrow</span></a></p></td>
<td>1</td>
<td>1</td>
<td><p>128,67</p>
<p>(155,57)</p></td>
<td>128,67</td>
<td>643,35</td>
<td>1286,70</td>
</tr>
<tr class="even">
<td>Coral Camera Module</td>
<td><p><a href="https://www.seeedstudio.com/Coral-Camera-Module-p-2914.html"><span class="underline">Seeed</span></a></p>
<p><a href="https://www.arrow.com/en/products/g840-00180-01/google-corporation"><span class="underline">Arrow</span></a></p></td>
<td>1</td>
<td>1</td>
<td><p>25,71</p>
<p>(27,84)</p></td>
<td>25,71</td>
<td>128,55</td>
<td>257,10</td>
</tr>
<tr class="odd">
<td>Deans connector</td>
<td><a href="https://www.amazon.ca/-/fr/UEETEK-paires-connecteurs-ultra-batterie/dp/B077TXMTJZ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"><span class="underline">Amazon</span></a><br />
<a href="https://www.amazon.ca/paires-connecteurs-femelles-silicone-batterie/dp/B07WHPD4KD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"><span class="underline">Amazon</span></a></td>
<td>1</td>
<td><p>10</p>
<p>5</p></td>
<td><p>11,99</p>
<p>(12,99)</p></td>
<td>11,99</td>
<td>11,99</td>
<td>11,99</td>
</tr>
<tr class="even">
<td>Lipo 2S 2000mAh</td>
<td><a href="https://www.amazon.ca/-/fr/Hosim-Batterie-rechargeable-25-DJ02-%C3%89chelle/dp/B07SW2K4P4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"><span class="underline">Amazon</span></a></td>
<td>2</td>
<td>1</td>
<td>25,98</td>
<td>51,96</td>
<td>259,80</td>
<td>519,60</td>
</tr>
<tr class="odd">
<td>M2 Screw 4mm</td>
<td><p><a href="https://www.cyclonefpv.com/products/m2-drone-screws-socket-head-cap-9-sizes-100-count-steel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"><span class="underline">CycloneFPV</span></a></p>
<p><a href="https://rotorvillage.ca/m2-x-5mm-black-steel-button-head-screw-8pk/"><span class="underline">RotorVillage</span></a><br />
<a href="https://www.amazon.ca/-/fr/XunLiu-molet%C3%A9es-hexagonale-alliage-dacier/dp/B07CHM7ZQK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"><span class="underline">Amazon</span></a></p></td>
<td><p>2</p>
<p>2</p>
<p>1</p></td>
<td><p>1</p>
<p>1</p>
<p>6</p></td>
<td><p>1,27</p>
<p>(2,49)</p>
<p>(46,06)</p></td>
<td>2,54</td>
<td>12,70</td>
<td>25,40</td>
</tr>
<tr class="even">
<td>M2 Screw 16mm</td>
<td><p><a href="https://www.cyclonefpv.com/products/m2-drone-screws-socket-head-cap-9-sizes-100-count-steel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"><span class="underline">CycloneFPV</span></a></p>
<p><a href="https://rotorvillage.ca/m2-x-16mm-black-steel-button-head-screw-8pk/"><span class="underline">RotorVillage</span></a></p>
<p><a href="https://www.amazon.ca/-/fr/XunLiu-molet%C3%A9es-hexagonale-alliage-dacier/dp/B07CHGZT5K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"><span class="underline">Amazon</span></a></p></td>
<td><p>1</p>
<p>1</p></td>
<td><p>1</p>
<p>16</p></td>
<td><p>1,27</p>
<p>(2,79)</p>
<p>(11,79)</p></td>
<td>1,27</td>
<td>6,35</td>
<td>12,70</td>
</tr>
<tr class="odd">
<td>Wire 28/32 AWG</td>
<td><a href="https://www.amazon.ca/1007-Bo%C3%AEte-solide-avec-%C3%A9lectriques/dp/B073RDGTPB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"><span class="underline">Amazon</span></a></td>
<td>1</td>
<td>15+</td>
<td>19,88</td>
<td>19,88</td>
<td>19,88</td>
<td>19,88</td>
</tr>
<tr class="even">
<td>Electrical tape</td>
<td><a href="https://www.amazon.ca/-/fr/Temflex-TEMFLEX-3-4X60-adh%C3%A9sif-%C3%A9lectrique/dp/B003DXV9HY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"><span class="underline">Amazon</span></a></td>
<td>1</td>
<td>15+</td>
<td>1,24</td>
<td>1,24</td>
<td>1,24</td>
<td>1,24</td>
</tr>
<tr class="odd">
<td>Hot glue</td>
<td><a href="https://www.amazon.ca/-/fr/Adtech-W220-34ZIP30-b%C3%A2tons-colle-chaude/dp/B00009RUCS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"><span class="underline">Amazon</span></a></td>
<td>1</td>
<td>15+</td>
<td>7,99</td>
<td>7,99</td>
<td>7,99</td>
<td>7,99</td>
</tr>
<tr class="even">
<td colspan="5">Total</td>
<td>478,21</td>
<td>1871,27</td>
<td>3619,03</td>
</tr>
<tr class="odd">
<td colspan="5">Unit total</td>
<td>478,21</td>
<td>374,254</td>
<td>361,903</td>
</tr>
</tbody>
</table>

The Coral board has the same connection than the Raspberry Pi Zero and
includes a memory, which allows to get rid of the SD card. It has better
performance and can do image processing as it would be with the vision
bonnet. More details about using the Coral Dev Mini can be found [here](https://git.mistlab.ca/oduguay/Coral_Cognifly).

When not highlighted in red or brown, the shipping should be from 1 day
to two weeks, depending on the selected option on the order. The
availability of the links may change and would need some more research
to find the same components.

The price does not include the shipping apart from the raspberry pi
alone as each order (on Canakit; one Pi at a time) must be shipped
separately. The price can be cheaper than shown on this document,
particularly for building a little number of drones, as you may already
have some component (for example the PLA filament) or if you find some
website shipping smaller quantities (for example connectors). Two
batteries have been considered per drone to allow more flight
flexibility, but you may want to have more or less of those.

Be aware that some components can be difficult to find and may increase
a lot the price or the shipping time if not available on the first
website suggested on the tables (used to calculate the total price).
This is the case for the Raspberry Pi Zero W and the Matek Optical Flow.
For the Coral boards and cameras, there can be restricted shipping areas
and may not ship to Canada.

While waiting for the longest shipping orders, you may want to print the
parts of the drones. For the TPU joints, it takes around 8 hours per
drone, and for the PLA, you will do at least two prints per drone of
around 4 hours each because some pieces need supports and others do not.

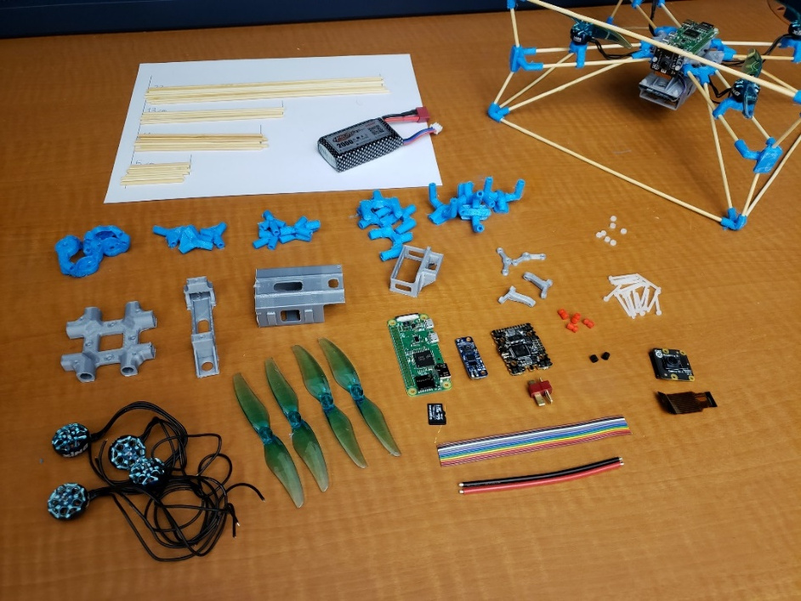
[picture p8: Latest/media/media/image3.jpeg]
Une image contenant texte Description générée automatiquement


## Building the drone

### Frame

The frame is built with wood sticks, flexible plastics joints, and hard
plastic base. Wood stick can be replaced with carbon rods, leading to a
more resistant but heavier drone. Note that cutting carbon requires
precautions and longer manufacturing time.

**Step 1**

Print the joints with TPU95a filament setting the following
configuration:

  - 100% infill density

  - No printing supports

  - No build plate adhesion

  - 228°C printing temperature (verify with your TPU filament)

  - 35mm/s printing speed (verify with your TPU filament)

**Table 5: Joints made from TPU95a**

| Joint  | 3D part | Quantity | Joint  | 3D part | Quantity |
| --- | --- | --- | --- | --- | --- |
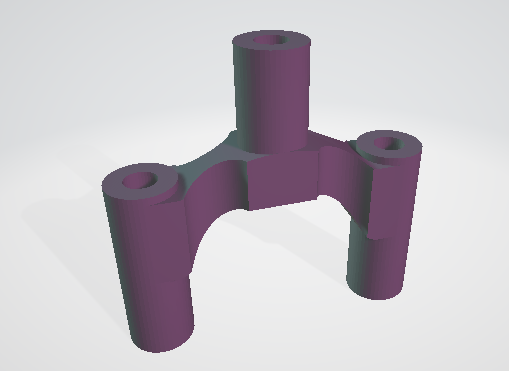
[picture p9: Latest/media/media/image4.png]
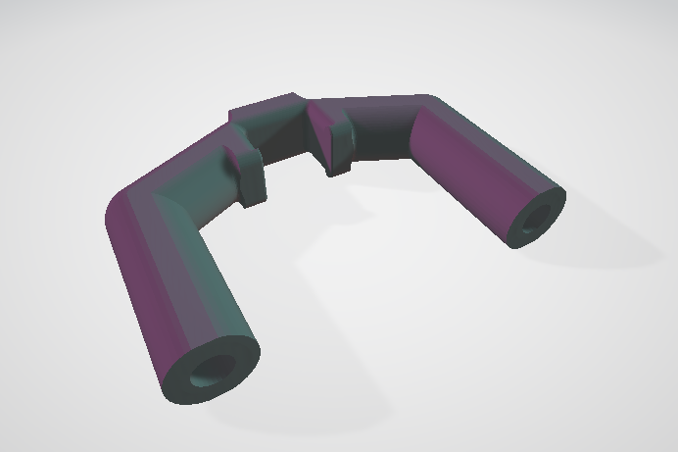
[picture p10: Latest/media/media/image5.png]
| TPU\_1 |  | 4 | TPU\_4 |  | 4 |
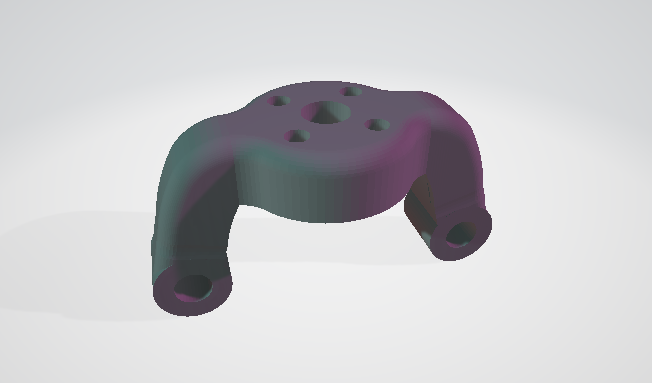
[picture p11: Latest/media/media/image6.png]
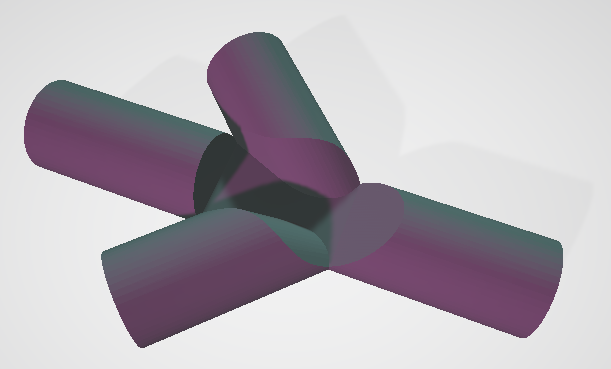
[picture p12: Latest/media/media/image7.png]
| TPU\_2 |  | 4 | TPU\_5 |  | 4 |
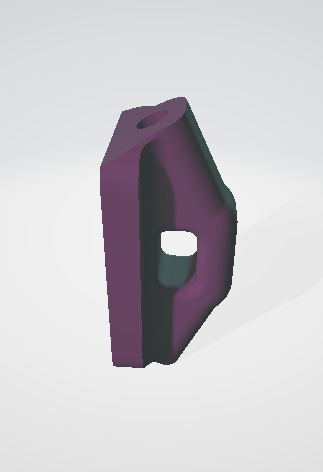
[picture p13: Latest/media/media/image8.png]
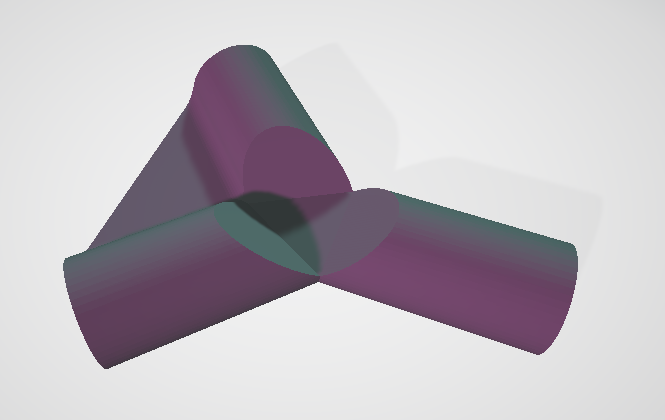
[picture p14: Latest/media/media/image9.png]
| TPU\_3 |  | 4 | TPU\_6 |  | 4 |

Make sure to orient each part as shown in the figure 1. The printing
time is 7h20 with the normal profile.

*Figure 1: Layout of TPU parts on Ultimaker 3.*

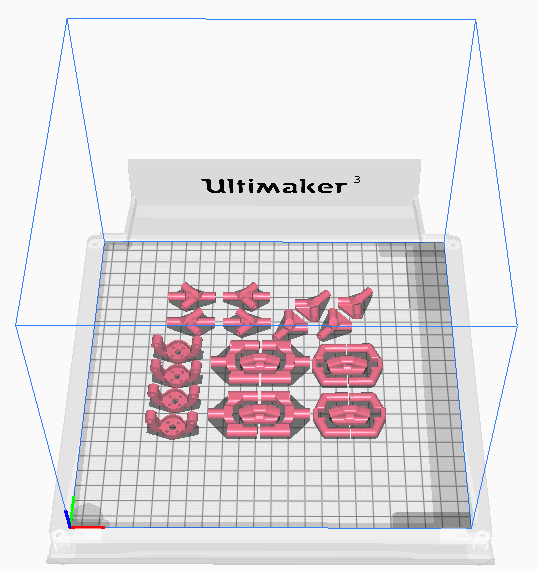
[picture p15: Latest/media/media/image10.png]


**Step 2**

Print the hard parts with PLA filament setting the following
configuration:

  - 10% infill density

  - No printing supports for PLA\_1, With printing supports for other
    parts

  - 200°C printing temperature (verify with your PLA filament)

  - 60mm/s printing speed (verify with your PLA filament)

**Table 6: Joints made from PLA**

| Joint  | 3D part | Quantity | Joint  | 3D part | Quantity |
| --- | --- | --- | --- | --- | --- |
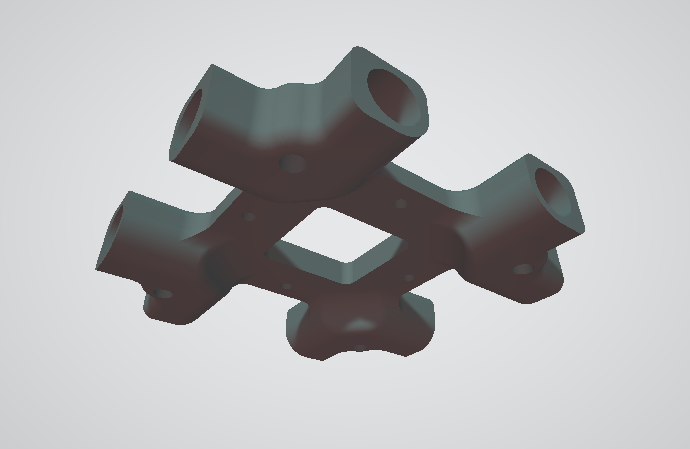
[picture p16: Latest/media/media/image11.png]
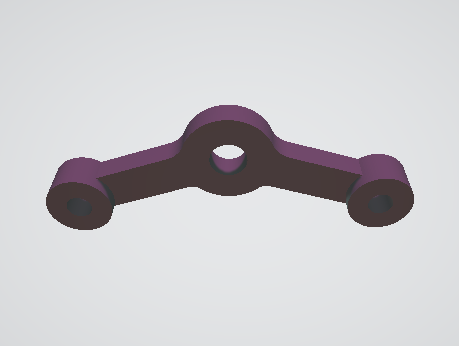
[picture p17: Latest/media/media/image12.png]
| PLA\_1 |  | 1 | PLA\_5 |  | 2 |
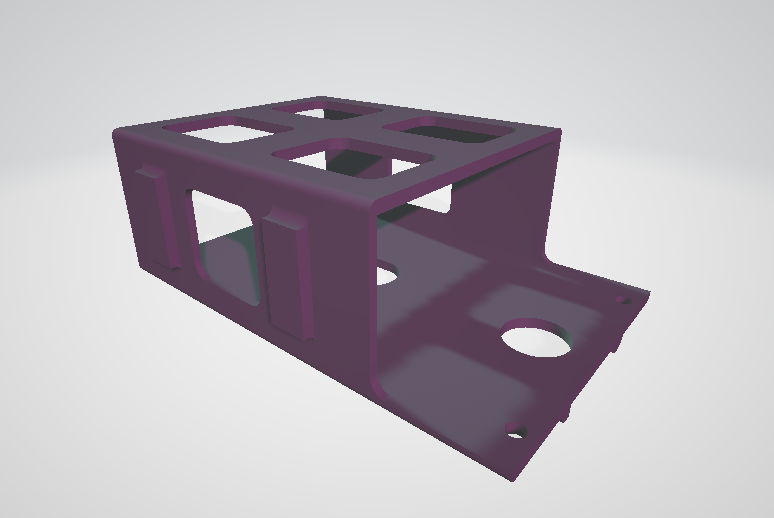
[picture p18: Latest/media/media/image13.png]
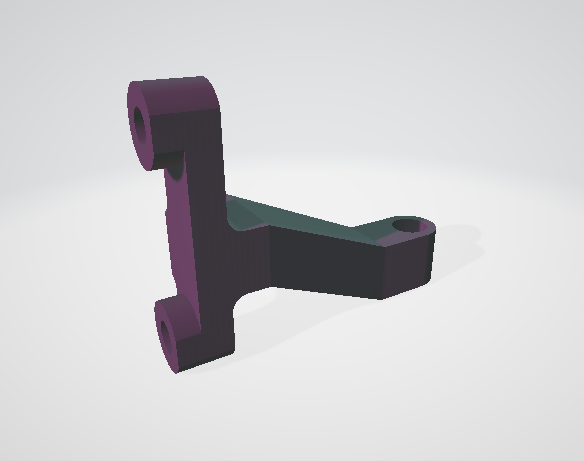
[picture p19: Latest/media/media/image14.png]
| PLA\_2 |  | 1 | PLA\_6 |  | 1 |
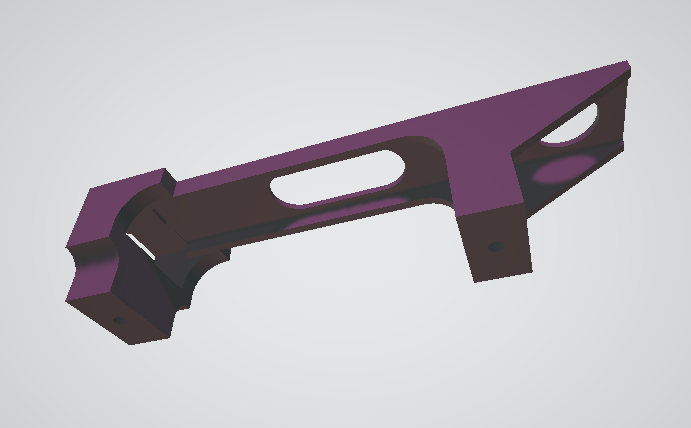
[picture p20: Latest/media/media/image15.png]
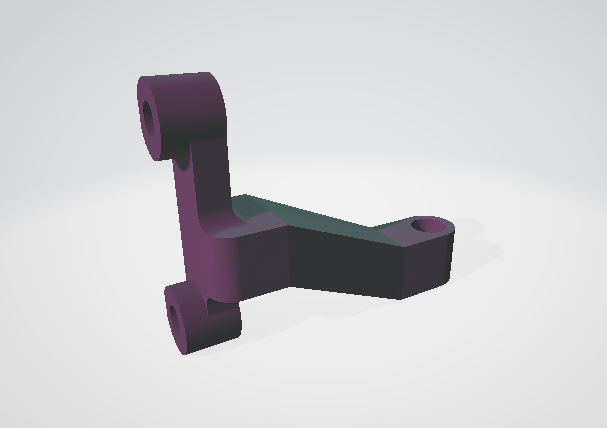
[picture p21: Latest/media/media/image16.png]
| PLA\_3 |  | 1 | PLA\_7 |  | 1 |
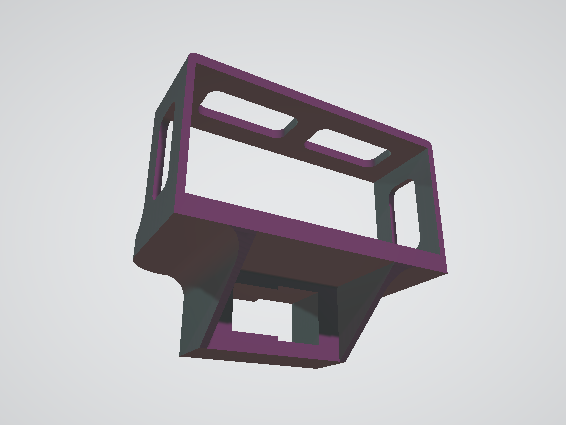
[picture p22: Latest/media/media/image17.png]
| PLA\_4 |  | Number of batteries | | | |

Orientation of the parts in the printer are shown in figure 2. The
printing time is 1h35 for the PLA\_1 part (without printing supports)
and 4h46 for the other PLA parts (with printing support).

*Figure 2: Layout of PLA parts on Ultimaker 3*

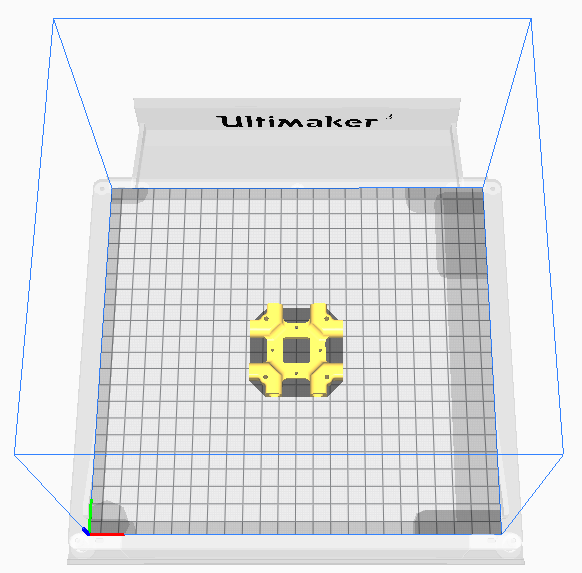
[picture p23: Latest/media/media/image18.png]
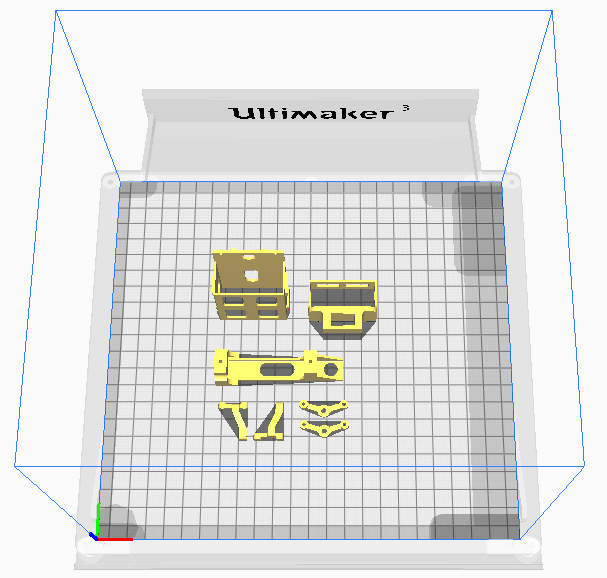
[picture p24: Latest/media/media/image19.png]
 

**Step 3**

Cut the sticks with a cutting pliers for wood frame of with a suitable
saw for carbon frame, to the dimensions written in table 6.

*Table 6: Stick dimensions and quantities for one drone*

| Dimension | Quantity |
| --- | --- |
| 23 cm | 8 |
| 13 cm | 4 |
| 11 cm | 8 |
| 5 cm | 8 |

**Step 4**

Insert the TPU\_4 part into the TPU\_3 central hole, you will need a
thin flat or round pliers. Reproduce the operations illustrated in the
figure 3.

*Figure 3: Insertion process of the joint (TPU\_4 into TPU\_3)*

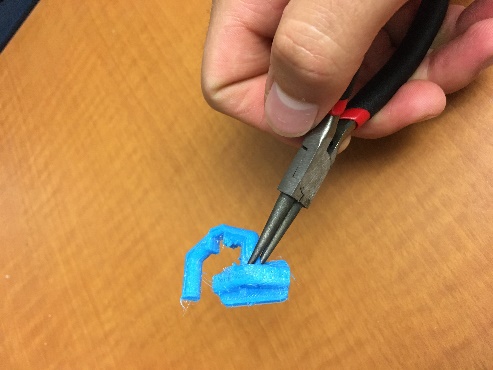
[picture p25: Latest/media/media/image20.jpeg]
Une image contenant outil, clé Description générée automatiquement
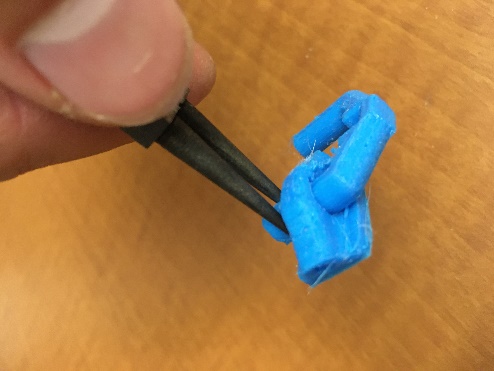
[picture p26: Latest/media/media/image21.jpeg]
Une image contenant personne Description générée automatiquement
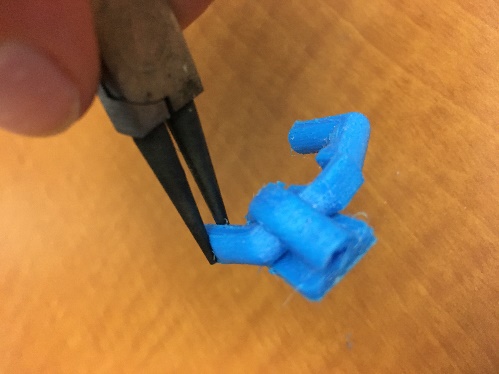
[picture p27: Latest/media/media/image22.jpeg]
Une image contenant plancher, intérieur, objets métalliques Description générée automatiquement
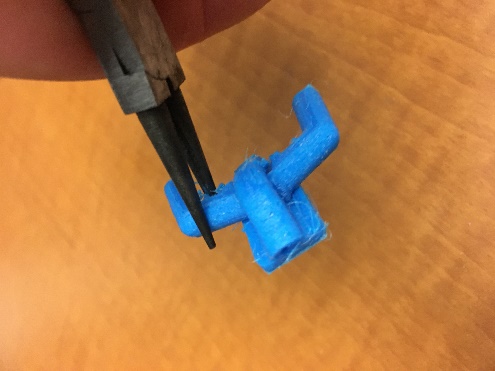
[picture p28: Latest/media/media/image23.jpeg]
Une image contenant plancher, intérieur Description générée automatiquement
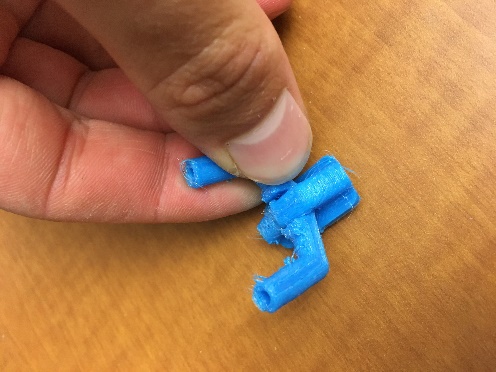
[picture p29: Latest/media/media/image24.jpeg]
Une image contenant personne, intérieur, main, accessoire Description générée automatiquement
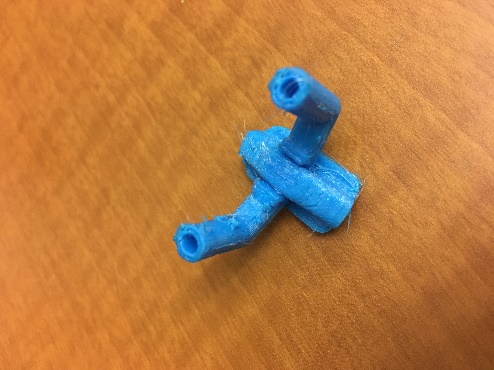
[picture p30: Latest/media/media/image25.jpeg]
Une image contenant plancher, objets métalliques, clé Description générée automatiquement


Do this operation with the four groups of joint (for one drone).

**Step 5**

You have now all the component to build the frame. Figure 4 shows them
for the assembly of one drone.

*Figure 4: Frame components*

Une image contenant texte Description générée automatiquement

Now insert the sticks into the joints as follow. All steps are
illustrated with images.

1)  Insert the 11cm sticks into external hole of TPU\_1 joint.



2)  Insert the 13cm sticks into the middle hole of TPU\_1 joint.



3)  Insert the TPU\_2 joint into the 11cm sticks from current assembly.

Une image contenant plancher, intérieur, bois Description générée automatiquement

4)  Insert the TPU\_4 into the other ends of the 11cm sticks from
    current assembly.

Une image contenant plancher, personne, intérieur Description générée automatiquement

5)  Insert the 5cm sticks into the holes of the TPU\_3 from current
    assembly.

Une image contenant plancher, intérieur Description générée automatiquement

6)  Insert the long foot of TPU\_5 into the 5cm stick as shown below.

Une image contenant plancher, intérieur, bleu Description générée automatiquement

7)  Insert the middle short foot of TPU\_5 into the 13cm stick.



8)  Insert the TPU\_6 into the other 5cm stick from current assembly.

Une image contenant plancher, jouet, bleu Description générée automatiquement

9)  Redo steps 1 to 8 three other times to get four assemblies.



10) Insert the TPU\_1 of the first assembly into the sided holes of
    PLA\_1.

Une image contenant personne, ciseaux, coupant, plancher Description générée automatiquement

11) Redo step 10 with each assembly.



12) Insert a 23cm stick into the remaining holes of a TPU\_5 part.



13) Redo step 12 for all TPU\_5 parts to complete the bottom of the
    frame.



14) Insert the last 23cm sticks into TPU\_6 parts to complete the top of
    the frame.



15) Glue the wood sticks to every TPU joints. Don’t glue the TPU\_1
    joints to the PLA\_1 part, it will allow to pass the wires and
    easier fix.



### Electronics

The electronics of the drone need to be soldered into the flight
controller (FC). The Optical flow sensor and the Raspberry Pi Zero W use
the UART ports, and the motors are connected with three wires each into
the ESC (integrated to the flight controller board).

**Step 6**

Take the flight controller, the Raspberry Pi, the Optical Flow, the four
motors, the Deans connector, the part PLA\_2 and PLA\_3, and the wires
as shown on the figure 5.

*Figure 5: Electronics components*



Connect all the components to the flight controller as following.

1)  Solder the Deans connector with the black and red wires from the FC
    package. Make sure to respect polarity as shown on the picture

 

2)  Insert the wires of the connector into the PLA\_3 part and glue the
    connector with hot glue. You can cut the wires to have a length of
    approximately 5cm.

 

3)  Solder the wires on the + (red) and – (black) connection of the
    flight controller.



4)  Take the AWG28 wires and cut them of approximately 10cm. Put some
    flux and tin on the following connectors of the FC: TX2; RX2; TX6;
    RX6; 4.5V; 5V; Ground (2) and all motors connectors.

 

5)  Solder the AWG28 wires on the connectors of the FC you prepared in
    previous step. Help you with the pictures.



The UART2 (TX2 and RX2) will be connected to the optical flow and UART6
(TX6 and RX6) will be connected to the Raspberry Pi. Before you decide
to change the ports, note that the Raspberry Pi has to be connected to
UART6 to work properly.

6)  Cut the wires of the motors about 8cm long and solder them on the
    flight controller. Note that in the straight condition (propellers
    facing up and the arrow of the FC facing up, pointing forward), the
    wires of the motors are not crossing except for motor 3 (indicated
    on FC) which should have two wires inverted. This should guarantee
    the motors to spin in the good orientation. Help you with the
    following picture to follow the wires.





7)  Solder the optical flow. Connect the TX of the optical flow to RX2
    on the FC; the RX of the optical flow with the TX2 on the FC; the
    ground together and the 5V of the optical flow to the 4.5V of the
    FC.



8)  Solder the Raspberry Pi. Connect the 5V of the FC to the PIN2 (upper
    left connector when facing down), the ground to PIN6 (the third left
    connector), the RX6 of optical flow to PIN8 (fourth left connector)
    and TX6 of optical flow to PIN10 (fifth left connector).



9)  Glue the PLA\_2 part to the PLA\_3 part with hot glue as shown in
    the following figure.



### Putting everything together

Now the electronics have to be mounted on the frame, the hardware will
then be all set for the drone.

**Step 7**

Take the built frame, the electronics, the propellers, the screws, the
rubber spacers, the PLA\_5, PLA\_6 and PLA\_7 parts, as shown in figure
6.

*Figure 6: Hardware components*



1)  Insert the 16mm screws into the four holes of the flight controller
    from bottom, then insert four rubber spacers into the screws from
    the top of the flight controller.



2)  Screw the 16mm screws into PLA\_1 so that the spacers begin to be
    compressed.



3)  Insert a 16mm screw in each PLA\_5 part, put it into the two holes
    of PLA\_1 part aligned with the Deans connector. Then screw them
    into the PLA\_3 part. Make sure to not stuck the small wires.



4)  Remove the TPU\_1 joint of Raspberry Pi’s wires side from the PLA\_1
    part. Put the wires into the free space of TPU\_1, as shown int the
    following figure. Then reinsert TPU\_1 joint.



5)  Screw the optical flow into PLA\_2 part with the 7mm screw coming
    with the motors package. Insert a rubber spacer between the optical
    flow and PLA\_2.

 

6)  Put the motors at their respective place by passing them through the
    wood sticks, then screw them with the 4mm screws into each TPU\_2
    parts. 
    
    **_ATTENTION:_ Don't apply too much torque on the screws or they may compress the TPU part, go too deep, hit the coils and damage the motor! Also, double check if the screws will not touch the coils because it's easy to mix screws of different sizes.**

 

7)  Screw the Raspberry Pi with the 7mm screws (coming with the motor
    package) to the PLA\_5 parts. Make sure the camera connector of the
    Raspberry Pi is facing the front (Optical Flow side), while
    inserting the PLA\_6 and PLA\_7 parts at the front and two rubber
    spacers at the back. Refer to the following figure.

 

8)  Screw the CW propellers with two 7mm screws each (from the motors
    package), at the front left and the back right of the drone, and the
    CCW propellers at the front right and the back left.

 

9)  Push the TPU\_2 parts across the wood sticks to make sure there is a
    gap of around 1cm between the propellers and the frame.



**Step 8**

Last step to complete the assembly of the drone, you must connect the Pi
camera and prepare the batteries.

1)  Put electric tape around the top of the LiPo battery (it will allow
    to glue the PLA support not directly on the battery).

Une image contenant texte Description générée automatiquement
You may
2)  Insert the PLA\_4 in the orientation shown in the following picture.
    The connector side on the PLA\_4 should be the same side than the
    brand on the battery.

Une image contenant texte Description générée automatiquement Une image contenant outil Description générée automatiquement

3)  Insert the Deans connector into the hole of PLA\_4 part. You may use
    pliers to put it in place, **but be careful not to short-circuit the battery terminals or damage it**.

 

4)  Put hot glue between the PLA\_4 part and the battery (side of the
    connector). You must fill the gap with glue while maintaining the
    PLA\_4 part in a position where the Dean connector is horizontal.
    This will allow a smooth insertion of the battery in the drone.

Une image contenant plancher Description générée automatiquement

5)  Redo steps 1 to 4 for the number of batteries you want to use.

**Safety precaution and troubleshooting**:  
Before connecting the battery
to the drone, it is suggested to verify with a multimeter the input and
outputs power connectors of the flight controller. If a short circuit is
detected, don’t connect the battery, and verify/redo soldering. If
verification is successful, connect the battery to the drone and make sure
flight controller is lightning up. If not, disconnect the battery
immediately and touch carefully the chip of flight controller to see if
it is overheating. If it's abnormally hot, this may indicate a short circuit
with low voltage outputs, otherwise, it could be RX/TX connections.

One extra suggestion is to wear safety glasses when operating the drone 
because the motors spin at high speeds and a faulty propeller could shatter projecting 
plastic bits towards your eyes.

*Figure 7: Camera Components*



6)  Connect the camera cable to the Pi camera.



7)  Connect the other side of the camera cable to the Raspberry Pi Zero
    of the drone.

Une image contenant équipement électronique Description générée automatiquement

8)  Screw the Pi camera with four 7mm screws (from the motors package)
    on the PLA\_6 and PLA\_7 supports.



The hardware of the drone is now ready. Next step will be to setup the
firmware and the configuration of the fight controller with INAV and the
files on the Raspberry Pi.

Une image contenant plancher Description générée automatiquement


## Software setup

### INAV

The configuration of the flight controller is made with INAV. It is an
open-source firmware compatible with a wide range of flight controllers.
It allows to link the different channels to the hardware connections,
and to set the different features of the drones. The firmware developed
specifically for CogniFly requires INAV version 2.3.2, software can be
downloaded on computer
[<span class="underline">here</span>](https://github.com/iNavFlight/inav-configurator/releases/tag/2.3.2).
Setup files and general instruction can be found on
[<span class="underline">GitHub</span>](https://github.com/thecognifly/cognifly-python/blob/main/readme/DRONE_SETUP.md).

**Step 1**

Open *inav-configurator.exe* from the INAV 2.3 and go to *Firmware
flasher* tab. Connect the flight controller of the drone with a
micro-USB cable to the computer.

Une image contenant table Description générée automatiquement Une image contenant texte, capture d’écran, moniteur, plusieurs Description générée automatiquement

**Step 2**

Click on *Load Firmware \[Local\]* and select the firmware file
*cognifly\_framework.hex* which can be downloaded
[<span class="underline">here</span>](https://github.com/thecognifly/cognifly-python/releases/download/v0.0.4/cognifly_framework.hex).
Make sure full chip erase is selected. Then, click on *Flash Firmware*,
the flight controller should turn automatically in DFU mode to flash the
firmware.

Une image contenant texte Description générée automatiquement

The loading bar will first erase the content of the chip then flash it.
You should see Programming successful at the end of this process.



**Step 3**

Click on the Connect blue icon on the top right INAV window. The
connection port should automatically be detected.



**Step 4**

Go to *CLI* tab (last tab on the left menu) and click on Load from file.
Select the CLI configuration file *cognifly\_configuration.txt*, which
can be downloaded
[<span class="underline">here</span>](https://github.com/thecognifly/cognifly-python/releases/download/v0.0.4/cognifly_configuration.txt).
Click Execute on the popped-up window.



Une image contenant texte, capture d’écran, moniteur, intérieur Description générée automatiquement

**Step 5**

After execution, type *save* in the text field and press enter, flight
controller will reboot.



**Step 6**

If the flight controller doesn’t reconnect automatically, click on the
connect button. You should see a representation of the drone in the
*setup* tab. Go to the *Outputs* tab, where you will be able to test the
motors. Make sure that the propellers are free to move and applied
required safety measure (if you are not confident with the building
process, you may begin by removing the propellers of the motor shafts).
Connect the battery to the drone and enable motor control.



**Step 7**

For the initial motor tests, ***remove the propellers***, hold safely the drone and increase slowly the control
bar of motor 1. If abnormal behaviour occurs, put back control bar to 0
and solve the issue. If motor is vibrating without turning, this may be
a sign of disconnected or shorted wires (verify soldering of the three
wires). If motor turns as expected, verify the direction of rotation of
the motor. If the right propeller is on it, simply verify that air is
pushed under the drone. If wires connection has been made as in building
process, the motor should turn in the right direction (Refer to INAV
image to find motor directions). If the motor is turning in the wrong
direction, two of the three wires need to be inverted (it doesn’t matter
which ones) by resoldering them on the flight controller (Before
disordering, double check that the right propellers is on the motor
shaft).

Une image contenant texte, portable, ordinateur, équipement électronique Description générée automatiquement

**Step 8**

Redo step 7 with motors 2, 3 and 4.

**Step 9**

Verify that flow and sonar icons on the top of the window are blue. If
not, it may be a sign of a bad connection (verify soldering) or wrong
port. If ports of optical flow and Raspberry Pi have been changed from
building process (by purpose or not), the new ports can be selected in
the *Ports* tab.



Une image contenant table Description générée automatiquement

**Step 10**

Go to the *Calibration* tab and calibrate on a level surface the drone
by clicking on *Calibrate Accelerometer*. Follow INAV instructions.
After accelerometer calibration done, calibrate the optical flow by
clicking on *Calibrate Optical Flow sensor*, following INAV instruction.

 Une image contenant texte Description générée automatiquement

**Step 11**

Go to *setup* tab and check the hardware health and configuration with
the pre-arming checks on the right of the window. (UAV is levelled
requires the drone to be hold horizontal).



INAV configuration is now completed

### Raspberry Pi Zero W

The configuration of the Raspberry Pi Zero is easily made loading a disk
image on the micro-SD card. It allows to execute Python programs
controlling the drone via Wi-Fi.

**Step 12**

Download
[<span class="underline">Raspbian</span>](https://www.raspberrypi.com/software/operating-systems/)
on the SD card using *Raspberry Pi OS Lite* image. If you already have a
local disk image of a previous CogniFly, it can be used to have the Wifi
configuration set. However, the name of the new CogniFly must be
changed.

**Step 13**

A software to create disk image is required. For windows, Win32 Disk
Imager can be downloaded
[<span class="underline">here</span>](https://sourceforge.net/projects/win32diskimager/).
Insert the micro-SD card via a micro-SD to SD or micro-SD to USB adapter
so computer can access it. Open Disk imager.

Browse the image file *…-raspios-bullseye-armhf-lite.img* or your local
file *PiZeroSD.img*. Verify that the device path is pointing to the
SD-card. The process will erase the content of the SD card. Then click
on *Write* and accept erasing the SD-card.

Une image contenant texte Description générée automatiquement Une image contenant texte Description générée automatiquement

After imaging process completed, two partitions should have been created
on SD card: *boot* and *rootfs*.

**Step 14**

Access the *boot* folder of the SD card and create a file without
extension named *ssh*.

***Linux system may be required to access the rootfs partition for the
following steps!***

**Step 15**

To configure the wpa-supplicant, edit
*/rootfs/etc/wpa\_supplicant/wpa\_supplicant.conf* file. (On linux, this
may require *sudo* command), adding the following (with the name of your
wifi connection) at the end of *wpa\_supplicant.conf*. Check the [troubleshooting section](readme.md#troubleshooting)
if you need extra information.

```
network={

ssid="yourNetworkSSID"

psk="yourNetworkPassword"

scan_ssid=1

}
```

**Step 16**

Change the name of the drone. Edit the */rootfs/etc/hostname* file by
replacing the default *raspberrypi* by desired drone name. Replace also
drone name in */rootfs/etc/hosts* file.

**Step 17**

Enable the pi camera and the UART serial port editing the
*/boot/config.txt* file under the *\[all\]* section, set the following
lines:
```
enable_uart=1 # serial port

start_x=1 # camera

gpu_mem=128 # camera
```

**Step 18**

Disable the console messages in the serial port editing the
*/boot/cmdline.txt* file. If you see *console=serial0,115200*, remove
this command. Raspberry Configuration is done.

**Step 19**

Plug the SD card into the Raspberry Pi. Plug a charged battery or
connect the Raspberry Pi with a micro-USB cable to a computer. Wait for
the Raspberry Pi to boot, the light should stop blinking.

**Step 20**

ssh the drone from your computer with the command *ssh
pi@myDroneName.local* (the default password should be raspberry). On
Windows, if ssh is not accessible from terminal,
[<span class="underline">Putty</span>](https://www.chiark.greenend.org.uk/~sgtatham/putty/latest.html)
software can be downloaded to establish the ssh connection.

**Step 21**

When Raspberry Pi successfully connected via ssh, execute the following
on the Raspberry Pi.
```
sudo apt-get update

sudo apt-get install libatlas-base-dev libopenjp2-7 libtiff5 python3-pip
```

**Step 22**

Install the cognifly-python library on the drone executing the following
command.

```
pip3 install --upgrade pip

pip3 install cognifly
```

The drone should now be ready to fly, see the section Usage on
[<span class="underline">cognifly-python
repository</span>](https://github.com/thecognifly/cognifly-python#installation)
to learn how to control the drone.

## Troubleshooting
### Wifi not working
The RPI allows the user to setup the connection by the creation of a file called ```wpa_supplicant.conf``` inside the boot partition (the only partition that will show on Windows computers when you read the SD card) and it will automatically connect in the next boot.

The beginning of the file ```wpa_supplicant.conf``` will have these lines:
```
ctrl_interface=DIR=/var/run/wpa_supplicant GROUP=netdev
update_config=1
country=<Insert 2 letter ISO 3166-1 country code here>
```
You must replace ```<Insert 2 letter ISO 3166-1 country code here>``` with your country code!

Just below the lines above, you need to use one of the patterns below according to the type of wifi network available for you (and don't forget to replace the characters between ```" "``` with your own stuff):
* ssid: wifi network name between ```" "```
* psk: wifi password between ```" "```

```
# 
# 1) Visible SSID with password
#
network={
	ssid="access_point_visible_ssid"
	psk="wifi-password"
	key_mgmt=WPA-PSK
	priority=20
	id_str="Hotspot"
}

#
# 2) Hidden SSID with password
#
network={
	ssid="access_point_hidden_ssid"
	scan_ssid=1
	psk="wifi-passpord"
	key_mgmt=WPA-PSK
	priority=10
	id_str="AP_Hidden_ssid"
}

#
# 3) Access point without password
#
network={
	ssid="access_point_without_pass"
	key_mgmt=NONE
	priority=5
	id_str="AP_No_Pass"
}
```
- [List of possible problems with solutions](https://support.thepihut.com/hc/en-us/articles/360014695877-Raspberry-Pi-won-t-connect-to-WiFi)
- [Setting up a headless Raspberry Pi](https://www.raspberrypi.com/documentation/computers/configuration.html#setting-up-a-headless-raspberry-pi)
### SSH not available
It's possible to enable SSH by simply creating an empty file named ```ssh.txt``` in the boot partition (the only partition that will show on Windows computers when you read the SD card). The RPI will enable SSH next time it boots.
- [More instructions about remote access](https://www.raspberrypi.com/documentation/computers/remote-access.html)
### Flashing the FC
- Double check you are using the correct firmware version.
- Make sure you set the flight controller to DFU mode before trying to flash a new firmware.

## Acknowledgements
Author of the original version of this manual: https://github.com/CharlesSol7

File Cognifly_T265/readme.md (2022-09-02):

# Building Instructions (Version 1)

The Cognifly is a drone with easy manufacturing, allowing
customization and autonomous flight. It has an optical flow and lidar,
allowing position and altitude hold, and a Raspberry Pi Zero 2W, allowing
wireless control and data processing. The
flight controller is working with INAV, which allows an easy
configuration of the drone.

This version of the cognifly features an intel realsense T265 camera for stabilization in challenging environments and the proper battery to support the additional weight. It can also use a crazyfly multiranger deck for onboard obstacle detection. 

The frame is built with wood sticks and resists to impact while flying.
Another configuration is possible with carbon fiber. It is highly recommended, as the frame can resist to more violent impacts (which can occur due to the increased weight of this version of the Cognifly). However, it is more
expensive and heavier. 

The carbon fiber version of CogniFly weighs 370g. It uses a LiPo battery 4S (14.8V, 130C) with a
1800mAh capacity, leading to a 10-minute flight time.

**Note** that the [Latest](../Latest/readme.md) version of the cognifly can be adapted to support the T265, by swapping the base mounts.



## Table of Contents
1. [Bill of Materials](readme.md#bill-of-materials)
    * [Table 1: Description of the hardware for one drone](readme.md#table-1-description-of-the-hardware-for-one-drone)
    * [Table 2: Bill of Materials using a Raspberry Pi zero 2W](readme.md#table-2-bill-of-materials-using-a-raspberry-pi-zero)
2. [Building the drone](readme.md#building-the-drone)
    * [Frame](readme.md#frame)
    * [Electronics](readme.md#electronics)
    * [Putting everything together](readme.md#putting-everything-together)
3. [Software setup](readme.md#software-setup)
    * [INAV](readme.md#inav)
    * [Raspberry Pi Zero 2W](readme.md#raspberry-pi-zero-w)
4. [Troubleshooting](readme.md#troubleshooting)
    * [Wifi not working](readme.md#wifi-not-working)
    * [ssh not available](readme.md#ssh-not-available)
    * [Flashing the FC](readme.md#flashing-the-fc)
    * [Motors overheating](readme.md#some-motors-overheat)
5. [Acknowledgements](readme.md#acknowledgements)

## Bill of Materials

To build this drone, some tools will be needed and not included in the
following list: a 3D printer (ideally two so you can print continuously
the TPU parts and the PLA parts for more than 1 drone), a soldering iron
with tin (and flux), a hot glue gun with glue, super glue, and a screwdriver for M2 & M3
screws, wire strippers, pliers…

### *Table 1: Description of the hardware for one drone*

<table>
<thead>
<tr class="header">
<th>Part Number</th>
<th>Item</th>
<th>Description</th>
<th>Quantity</th>
</tr>
</thead>
<tbody>
<tr class="odd">
<td>CF01-CF04</td>
<td><p>Wood stick</p>
<p><em>Or carbon fibre rods</em></p></td>
<td><p>Frame</p>
<p>Diameter: 3mm; Length : &gt;25cm</p></td>
<td>20 sticks</td>
</tr>
<tr class="even">
<td>CF05-CF10</td>
<td>TPU95a filament</td>
<td><p>Frame (Joints)</p>
<p>TPU95a filament; flexible plastic parts</p></td>
<td>34g</td>
</tr>
<tr class="odd">
<td>CF11-CF17</td>
<td>PLA filament</td>
<td><p>Structure</p>
<p>PLA filament; Hard plastic parts</p></td>
<td>24g</td>
</tr>
<tr class="even">
<td><p>CF18A</p>
<p>CF18B</p></td>
<td>Motor XING2 1404 3000KV</td>
<td><p>Motor XING2 1404<br />
3000KV; 10,1g</p>
<p>(7mm screws included used for propellers, Raspberry Pi, and optical flow attachment)</p></td>
<td><p>4</p>
<p>(18)</p></td>
</tr>
<tr class="odd">
<td>CF19</td>
<td>Screw spacer</td>
<td>M2 Rubber Damping Ball (for the optical flow)</td>
<td>2</td>
</tr>
<tr class="even">
<td><p>CF20A</p>
<p>CF20B</p></td>
<td>FC – ESC JHEMCU GHF420 35A</td>
<td><p>20x20mm Jhemcu GHF420AIO F4 OSD Flight Controller w/ 5V 9V BEC Output &amp; Built-in 35A BL_S 4In1 Brushless ESC</p>
<p>(4 Rubber Damping Balls included used for FC attachment and connector to make power cables)</p></td>
<td><p>1</p>
<p>(4)</p></td>
</tr>
<tr class="odd">
<td>CF21-CF22</td>
<td>Propellers 4024</td>
<td>Gemfan Hurricane 4024 2 Blades</td>
<td>2CW and 2CCW</td>
</tr>
<tr class="even">
<td>CF23</td>
<td>Matek Optical Flow and Lidar</td>
<td>Matek Optical Flow &amp; Lidar Sensor - 3901-L0X</td>
<td>1</td>
</tr>
<tr class="odd">
<td>CF24</td>
<td>Raspberry Pi Zero 2W</td>
<td>Raspberry Pi Zero 2W (Wireless)</td>
<td>1</td>
</tr>
<tr class="even">
<td>CF25</td>
<td>SD card</td>
<td>Micro SD card &gt; 16Go</td>
<td>1</td>
</tr>
<tr class="odd">
<td>CF26</td>
<td>Lipo 4S 1800mAh</td>
<td>Sunpadow Lipo Battery Battery 4S; 1800 mAh; 7,4V 130C</td>
<td>1 or more</td>
</tr>
<tr class="even">
<td>CF27</td>
<td>M2 Screw 4mm</td>
<td>M2 Screw 4mm</td>
<td>16</td>
</tr>
<tr class="odd">
<td>CF28</td>
<td>M2 Screw 16mm</td>
<td>M2 Screw 16mm</td>
<td>6</td>
</tr>
<tr class="even">
<td>CF29</td>
<td>Wire 28/32 AWG</td>
<td>4 Wires 28/32 AWG (4 colors)</td>
<td>2X15cm</td>
</tr>
<tr class="odd">
<td>CF30</td>
<td>Intel realsense T265 camera</td>
<td>Camera for visual-inertial odometry</td>
<td>1</td>
</tr>

</tbody>
</table>

### *Table 2: Bill of Materials using a Raspberry Pi Zero 2W*

<table>
<thead>
<tr class="header">
<th>Item</th>
<th>Link Canada 2021</th>
<th>Quantity</th>
<th>Drone quantity</th>
<th>Price (CAD)</th>
<th>Price for one drone</th>
<th>Price for 5 drones</th>
<th>Price for 10 drones</th>
</tr>
</thead>
<tbody>
<tr class="odd">
<td>Wood stick</td>
<td><a href="https://www.amazon.ca/-/fr/Chef-Craft-brochettes-fines-bambou/dp/B075YFB1SZ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"><span class="underline">Amazon</span></a><br />
grocery store</td>
<td>1</td>
<td>6</td>
<td>8,67</td>
<td>8,67</td>
<td>8,67</td>
<td>17,34</td>
</tr>
<tr class="even">
<td>TPU95a filament</td>
<td><a href="https://www.amazon.ca/Polymaker-PolyFlex-Flexible-Filament-Dimensional/dp/B083XFT675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"><span class="underline">Amazon</span></a></td>
<td>1</td>
<td>15+</td>
<td>39,99</td>
<td>39,99</td>
<td>39,99</td>
<td>39,99</td>
</tr>
<tr class="odd">
<td>PLA filament</td>
<td><a href="https://www.amazon.ca/construction-pr%C3%A9cision-dimensionnelle-compatible-imprimantes/dp/B07PGZNM34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"><span class="underline">Amazon</span></a></td>
<td>1</td>
<td>15+</td>
<td>28,99</td>
<td>28,99</td>
<td>28,99</td>
<td>28,99</td>
</tr>
<tr class="even">
<td>Motor XING2 1404 3000KV</td>
<td><a href="https://shop.iflight-rc.com/motors-cat88/xing2-1404-toothpick-ultralight-build-unibell-pro1482"><span class="underline">Iflight</span></a><br />
<a href="https://www.banggood.com/IFlight-XING2-1404-3000KV-3800KV-4600KV-2-4S-Brushless-Motor-for-Toothpick-RC-Drone-FPV-Racing-p-1817793.html?ID=517763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"><span class="underline">Banggood</span></a></td>
<td>4</td>
<td>1</td>
<td>20,50<br />
(26,95)</td>
<td>20,50</td>
<td>102,50</td>
<td>205,00</td>
</tr>
<tr class="odd">
<td>Screw spacer</td>
<td><p><a href="https://shop.iflight-rc.com/m2-m3-rubber-damping-ball-for-f4-f7-32k-flight-control-40pcs-pro294?search=rubber"><span class="underline">iflight</span></a></p>
<p><a href="https://www.banggood.com/20-PCS-SupraRC-M2x4-M2-Anti-vibration-Standoff-Rubber-Damping-Ball-for-F7BT-Flight-Controller-ESC-RC-Drone-FPV-Racing-p-1716028.html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"><span class="underline">Banggood</span></a></p></td>
<td>1</td>
<td>10<br />
5</td>
<td>8,96<br />
(10,26)</td>
<td>8,96</td>
<td>8,96</td>
<td>8,96</td>
</tr>
<tr class="even">
<td>FC – ESC JHEMCU GHF420 35A</td>
<td><p><a href="https://www.cyclonefpv.com/products/jhemcu-ghf420-aio-20x20-fc-20a-and-30a-options?variant=32949263695915"><span class="underline">cycloneFPV</span></a></p>
<p><a href="https://rotorvillage.ca/jhemcu-ghf420-f4-35a-aio-flight-controller/"><span class="underline">RotorVillage</span></a></p>
<p><a href="https://www.banggood.com/20x20mm-Jhemcu-GHF420AIO-F4-OSD-Flight-Controller-w-or-5V-9V-BEC-Output-and-Built-in-35A-BL_S-4In1-Brushless-ESC-Support-DJI-Air-Unit-for-RC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"><span class="underline">Banggood</span></a></p></td>
<td>1</td>
<td>1</td>
<td><p>76,92</p>
<p>(83,99)</p>
<p>(92,42)</p></td>
<td>76,92</td>
<td>384,6</td>
<td>769,20</td>
</tr>
<tr class="odd">
<td>Propellers 4024</td>
<td><p><a href="https://www.cyclonefpv.com/collections/4-props/products/gemfan-hurricane-4024-2-blade-1408-1506-motor-props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"><span class="underline">CycloneFPV</span></a></p>
<p><a href="https://rotorvillage.ca/gemfan-4024-hurricane-prop/"><span class="underline">RotorVillage</span></a></p>
<p><a href="https://www.banggood.com/4-Pairs-Gemfan-Hurricane-4024-2-blade-4-Inch-PC-Propeller-for-1408-1506-Brushless-Motor-RC-Drone-FPV-Racing-p-1657418.html?ID=3237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"><span class="underline">Banggood</span></a></p></td>
<td>1</td>
<td>2</td>
<td><p>4,47</p>
<p>(5,49)</p>
<p>(10,26)</p></td>
<td>4,47</td>
<td>13,41</td>
<td>22,35</td>
</tr>
<tr class="even">
<td>Matek Optical Flow and Lidar</td>
<td><p><a href="https://www.getfpv.com/matek-optical-flow-lidar-sensor-3901-l0x.html"><span class="underline">GetFPV</span></a></p>
<p><a href="https://rotorvillage.ca/Matek-3901-L0X-Optical-Flow-Lidar-Sensor/"><span class="underline">RotorVillage</span></a></p>
<p><a href="https://www.amazon.ca/-/fr/Systems-3901-L0X-capteur-optique-quadrirotor/dp/B082LYQGDD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"><span class="underline">Amazon</span></a><br />
<a href="https://can.grandado.com/products/style-matek-system-optical-flow-lidar-sensor-3901-l0x-module-support-inav-for-rc-drone-fpv-racing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"><span class="underline">Grandado</span></a></p></td>
<td>1</td>
<td>1</td>
<td><p>38,46</p>
<p>(38,99)</p>
<p>(96,22)</p>
<p>(77,09)</p></td>
<td>38,46</td>
<td>192,30</td>
<td>384,60</td>
</tr>
<tr class="odd">
<td>Raspberry Pi Zero 2W</td>
<td><p><a href="https://www.cytron.io/p-raspberry-pi-zero-2-w"><span class="underline">Cytron</span></a></p>
<p><a href="https://www.pishop.co.za/store/raspberry-pi-zero-2-w"><span class="underline">Pishop</span></a></p>
</td>
<td>1</td>
<td>1</td>
<td><p>24,219</p>
<p>(22,29)</p></td>
<td>22,29</td>
<td>111,45</td>
<td>222,9</td>
</tr>
<tr class="even">
<td>Intel Realsense T265</td>
<td><p><a href="https://www.ebay.com/p/2302772770"><span class="underline">Ebay</span></a></p>
</td>
<td>1</td>
<td>1</td>
<td><p>477,5</p>
<td>477,5</td>
<td>2387,5</td>
<td>4775</td>
</tr>
<tr class="odd">
<td>SD card</td>
<td><p><a href="https://www.amazon.ca/Gigastone-cartes-surveillance-daction-professionnelle/dp/B07XB42B99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"><span class="underline">Amazon</span></a></p>
<p><a href="https://www.amazon.ca/-/fr/SanDisk-SDSQUAR-064G-GN6MA-m%C3%A9moire-microSDXC-adaptateur/dp/B073JYVKNX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"><span class="underline">Amazon</span></a></p></td>
<td><p>1</p>
<p>1</p></td>
<td><p>5</p>
<p>1</p></td>
<td><p>59,98</p>
<p>(15,39)</p></td>
<td>15,39</td>
<td>59,98</td>
<td>119,96</td>
</tr>
<tr class="even">
<td>Lipo 4S 1800mAh</td>
<td><a href="https://www.aliexpress.com/item/1005002303835558.html"><span class="underline">Aliexpress</span></a></td>
<td>2</td>
<td>1</td>
<td>18,01</td>
<td>36,02</td>
<td>180,1</td>
<td>360,2</td>
</tr>
<tr class="odd">
<td>M2 Screw 4mm</td>
<td><p><a href="https://www.cyclonefpv.com/products/m2-drone-screws-socket-head-cap-9-sizes-100-count-steel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"><span class="underline">CycloneFPV</span></a></p>
<p><a href="https://rotorvillage.ca/m2-x-5mm-black-steel-button-head-screw-8pk/"><span class="underline">RotorVillage</span></a><br />
<a href="https://www.amazon.ca/-/fr/XunLiu-molet%C3%A9es-hexagonale-alliage-dacier/dp/B07CHM7ZQK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"><span class="underline">Amazon</span></a></p></td>
<td><p>2</p>
<p>2</p>
<p>1</p></td>
<td><p>1</p>
<p>1</p>
<p>6</p></td>
<td><p>1,27</p>
<p>(2,49)</p>
<p>(46,06)</p></td>
<td>2,54</td>
<td>12,70</td>
<td>25,40</td>
</tr>
<tr class="even">
<td>M2 Screw 16mm</td>
<td><p><a href="https://www.cyclonefpv.com/products/m2-drone-screws-socket-head-cap-9-sizes-100-count-steel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"><span class="underline">CycloneFPV</span></a></p>
<p><a href="https://rotorvillage.ca/m2-x-16mm-black-steel-button-head-screw-8pk/"><span class="underline">RotorVillage</span></a></p>
<p><a href="https://www.amazon.ca/-/fr/XunLiu-molet%C3%A9es-hexagonale-alliage-dacier/dp/B07CHGZT5K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"><span class="underline">Amazon</span></a></p></td>
<td><p>1</p>
<p>1</p></td>
<td><p>1</p>
<p>16</p></td>
<td><p>1,27</p>
<p>(2,79)</p>
<p>(11,79)</p></td>
<td>1,27</td>
<td>6,35</td>
<td>12,70</td>
</tr>
<tr class="odd">
<td>Wire 28/32 AWG</td>
<td><a href="https://www.amazon.ca/1007-Bo%C3%AEte-solide-avec-%C3%A9lectriques/dp/B073RDGTPB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"><span class="underline">Amazon</span></a></td>
<td>1</td>
<td>15+</td>
<td>19,88</td>
<td>19,88</td>
<td>19,88</td>
<td>19,88</td>
</tr>
<tr class="even">
<td>Electrical tape</td>
<td><a href="https://www.amazon.ca/-/fr/Temflex-TEMFLEX-3-4X60-adh%C3%A9sif-%C3%A9lectrique/dp/B003DXV9HY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"><span class="underline">Amazon</span></a></td>
<td>1</td>
<td>15+</td>
<td>1,24</td>
<td>1,24</td>
<td>1,24</td>
<td>1,24</td>
</tr>
<tr class="odd">
<td>Hot glue</td>
<td><a href="https://www.amazon.ca/-/fr/Adtech-W220-34ZIP30-b%C3%A2tons-colle-chaude/dp/B00009RUCS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"><span class="underline">Amazon</span></a></td>
<td>1</td>
<td>15+</td>
<td>7,99</td>
<td>7,99</td>
<td>7,99</td>
<td>7,99</td>
</tr>
<tr class="even">
<td colspan="5">Total</td>
<td>802,15</td>
<td>4010,6</td>
<td>8021,2</td>
</tr>
<tr class="odd">
<td colspan="5">Unit total</td>
<td>802,15</td>
<td>695,07</td>
<td>695,07</td>
</tr>
</tbody>
</table>

The price does not include the shipping as each order must be shipped
separately. The price can be cheaper than shown on this document,
particularly for building a little number of drones, as you may already
have some component (for example the PLA filament) or if you find some
website shipping smaller quantities (for example connectors). It can also be more expensive due to the ongoing raspberry pi shortage. Two
batteries have been considered per drone to allow more flight
flexibility, but you may want to have more or less of those.

Be aware that some components can be difficult to find and may increase
a lot the price or the shipping time if not available on the first
website suggested on the tables (used to calculate the total price).
This is the case for the Raspberry Pi Zero 2W and the Matek Optical Flow.

While waiting for the longest shipping orders, you may want to print the
parts of the drones. 

## Notes on building

It is advised to go through the software setup as you build the Cognifly, to test the components. For instance, as soon as you solder the optical flow to the FC, check on INAV that there are no hardware health issues. You can also test that the raspberry pi can connect to the FC, using the cognifly-controller script (just by connecting the FC to your computer) after having connected the rapsberry pi and the FC.

## Building the drone

### Frame

The frame is built with wood sticks, flexible plastics joints, and hard
plastic base. Wood stick can be replaced with carbon rods, leading to a
more resistant but heavier drone. Note that cutting carbon requires
precautions and longer manufacturing time.

**Step 1**

Print the joints with TPU95a filament setting the following
configuration:

  - 100% infill density

  - No printing supports

  - No build plate adhesion

  - 228°C printing temperature (verify with your TPU filament)

  - 35mm/s printing speed (verify with your TPU filament)

**Table 5: Joints made from TPU95a**

| Joint  | 3D part | Quantity | Joint  | 3D part | Quantity |
| --- | --- | --- | --- | --- | --- |
| TPU\_1 |  | 4 | TPU\_4 |  | 4 |
| TPU\_2 |  | 4 | TPU\_5 |  | 4 |
| TPU\_3 |  | 4 | TPU\_6 |  | 4 |

Make sure to orient each part as shown in the figure 1. The printing
time is 7h20 with the normal profile.

*Figure 1: Layout of TPU parts on Ultimaker 3.*



**Step 2**

Print the hard parts with PLA filament setting the following
configuration:

  - 10% infill density

  - No printing supports for PLA\_1, With printing supports for other
    parts

  - 200°C to 235°C printing temperature (verify with your PLA filament)

  - 60mm/s printing speed (verify with your PLA filament)

**Table 6: Joints made from PLA**

| Joint  | 3D part | Quantity | Joint  | 3D part | Quantity |
| --- | --- | --- | --- | --- | --- |
| PLA\_1 |  | 1 | PLA\_5 |  | 2 |
| PLA\_2 |  | 1 | PLA\_6 |  | 1 |
| PLA\_3 |  | 1 | PLA\_7 |  | 1 |
| PLA\_4 |  | 1 | PLA\_8 |  | 4 |
| PLA\_9 |  | 1 

Orientation of the parts in the printer are shown in figure 2. The
printing time is 1h35 for the PLA\_1 part (without printing supports)
and 4h10 for the other PLA parts (except the battery case). The printing time of the battery case is 4h16.

*Figure 2: Layout of PLA parts on Ultimaker 3*

  

**Step 3**

Cut the sticks with a cutting pliers for wood frame of with a suitable
saw for carbon frame, to the dimensions written in table 6.

*Table 6: Stick dimensions and quantities for one drone*

| Dimension | Quantity |
| --- | --- |
| 23 cm | 8 |
| 13 cm | 4 |
| 11 cm | 8 |
| 5 cm | 8 |

**Step 4**

Insert the TPU\_4 part into the TPU\_3 central hole, you will need a
thin flat or round pliers. Reproduce the operations illustrated in the
figure 3.

*Figure 3: Insertion process of the joint (TPU\_4 into TPU\_3)*

Une image contenant outil, clé Description générée automatiquementUne image contenant personne Description générée automatiquementUne image contenant plancher, intérieur, objets métalliques Description générée automatiquementUne image contenant plancher, intérieur Description générée automatiquementUne image contenant personne, intérieur, main, accessoire Description générée automatiquementUne image contenant plancher, objets métalliques, clé Description générée automatiquement

Do this operation with the four groups of joint (for one drone).

**Step 5**

You have now all the component to build the frame. Figure 4 shows them
for the assembly of one drone.

*Figure 4: Frame components*

Une image contenant texte Description générée automatiquement

Now insert the sticks into the joints as follow. All steps are
illustrated with images.

1)  Insert the 11cm sticks into external hole of TPU\_1 joint.



2)  Insert the 13cm sticks into the middle hole of TPU\_1 joint.



3)  Insert the TPU\_2 joint into the 11cm sticks from current assembly.

Une image contenant plancher, intérieur, bois Description générée automatiquement

4)  Insert the TPU\_4 into the other ends of the 11cm sticks from
    current assembly.

Une image contenant plancher, personne, intérieur Description générée automatiquement

5)  Insert the 5cm sticks into the holes of the TPU\_3 from current
    assembly.

Une image contenant plancher, intérieur Description générée automatiquement

6)  Insert the long foot of TPU\_5 into the 5cm stick as shown below.

Une image contenant plancher, intérieur, bleu Description générée automatiquement

7)  Insert the middle short foot of TPU\_5 into the 13cm stick.



8)  Insert the TPU\_6 into the other 5cm stick from current assembly.

Une image contenant plancher, jouet, bleu Description générée automatiquement

9)  Redo steps 1 to 8 three other times to get four assemblies.



10) Insert the TPU\_1 of the first assembly into the sided holes of
    PLA\_1.

Une image contenant personne, ciseaux, coupant, plancher Description générée automatiquement

11) Redo step 10 with each assembly.



12) Insert a 23cm stick into the remaining holes of a TPU\_5 part.



13) Redo step 12 for all TPU\_5 parts to complete the bottom of the
    frame.



14) Insert the last 23cm sticks into TPU\_6 parts to complete the top of
    the frame.



15) Glue the wood sticks to every TPU joints. Don’t glue the TPU\_1
    joints to the PLA\_1 part, it will allow to pass the wires and
    easier fix.



16) Thread the holes of the column in the PLA_2 part using a 3mm thread. Be gentle to avoid breaking the columns. 

### Electronics

The electronics of the drone need to be soldered into the flight
controller (FC) and the raspberri pi. The multiranger communicates with the raspberry pi via i2C.

**Step 6**
Take the raspberry pi, the multiranger support (PLA_9), the multiranger deck and headers.

1) Remove any leftover support from the PLA_9 part. 



2) Press the headers into the two rectangular holes until they fit (not exceed the surface of PLA_9), then take them out. Put a bit of super glue inside the two rectangular holes, then press the headers until the glue dries.



3) Insert the multiranger deck on the headers.



4) Take the AG28 wires and cut them in 4 pieces of 15 cm. Solder them to the SDA, SCL, Ground and VCOM pins (see the [Multiranger Deck Schematics](https://www.bitcraze.io/documentation/hardware/multi_ranger_deck/multi-ranger-reve.pdf)) from the top of the headers. Solder the SDA and SCL to the raspberry pi's SDA and SCL, respectively. Solder the ground to the raspberry pi's ground and the VCOM to the raspberry pi's 5V voltage input.



The Optical flow sensor and the Raspberry Pi Zero 2W use
the UART ports, and the motors are connected with three wires each into
the ESC (integrated to the flight controller board).

**Step 7**

The Optical flow sensor and the Raspberry Pi Zero 2W use
the UART ports, and the motors are connected with three wires each into
the ESC (integrated to the flight controller board).

Take the flight controller, the Raspberry Pi, the Optical Flow, and the four
motors.

Note that this guide's Step 7 is the same as Step 6 in the [Latest](../Latest/readme.md#electronics) version (more detailed).

Connect all the components to the flight controller as following.

1)  Take the AWG28 wires and cut them of approximately 15cm. Put some
    flux and tin on the following connectors of the FC: TX2; RX2; TX6;
    RX6; 4.5V; 5V; Ground (2) and all motors connectors.

 

2)  Solder the AWG28 wires on the connectors of the FC you prepared in
    previous step. Help you with the pictures.



The UART2 (TX2 and RX2) will be connected to the optical flow and UART6
(TX6 and RX6) will be connected to the Raspberry Pi. Before you decide
to change the ports, note that the Raspberry Pi has to be connected to
UART6 to work properly.

3)  Solder the motor wires onto the FC. Note that in the straight condition (propellers
    facing up and the arrow of the FC facing up, pointing forward), the
    wires of the motors are not crossing except for motor 3 (indicated
    on FC) which should have two wires inverted. This should guarantee
    the motors to spin in the good orientation. Help you with the
    following picture to follow the wires. 
    
    Therefore, each motor (except motor 3), facing upwards (see picture below) has their outward wire connected to the outermost pad, the middle with the middle ones, and the inner ones with the inner ones respectively.
    Motor 3's outermost wire goes to the middle pad, and the outermost pad is connected to motor 3's middle wire.



4)  Solder the optical flow. Connect the TX of the optical flow to RX2
    on the FC; the RX of the optical flow with the TX2 on the FC; the
    ground together and the 5V of the optical flow to the 4.5V of the
    FC.

5)  Solder the Raspberry Pi. Connect the 5V of the FC to the PIN2 (upper
    left connector when facing down), the ground to PIN6 (the third left
    connector), the RX6 of optical flow to PIN8 (fourth left connector)
    and TX6 of optical flow to PIN10 (fifth left connector).



### Putting everything together

Now the electronics have to be mounted on the frame, the hardware will
then be all set for the drone.

**Step 8**

Take the built frame, the electronics, the propellers, the screws, the
rubber spacers, the PLA\_2 part.

1) Place the PLA\_2 above the screw holes of the PLA\_1 part.


2)  Insert the 16mm screws into the four holes of the flight controller through the FC, then insert four rubber spacers into the screws fbelow the FC. Orient the flight controller so that the micro USB port side of the FC faces the PLA\_1 part, and that the power input of the flight controller faces the direction of the 4 pillars of the PLA\_2 part.



3)  Screw the 16mm screws into PLA\_1 so that the spacers begin to be
    compressed.



4) Put the motors at their respective place by passing them through the
    wood sticks, then screw them with the screws from the motor package into each TPU\_2 through the PLA\_8
    parts. 

    **_ATTENTION:_ Don't apply too much torque on the screws or they may go too deep, hit the coils and damage the motor! Also, double check if the screws will not touch the coils because it's easy to mix screws of different sizes.**



5)  Insert a 16mm screw in each PLA\_5 part, put it into the two holes
    of PLA\_1 part.  Make sure to not stuck the small wires.
    If the screw is too lose, you can add a nut on the other side of the PLA\_1 part.



6)  Screw the optical flow into PLA\_2 part with the 16mm screws using a nut. Make sure that the optical flow is mounted in the same direction as the picture below, so that it will not be blocked later on by the T265 camera. Insert a rubber spacer between the optical
    flow and PLA\_2. Refer to the pictures below.

 

7)  Place the raspberry pi so that its camera slot faces direction of the optical flow. In case your wires are too short, you can remove the TPU\_1 joint of Raspberry Pi’s wires side from the PLA\_1. Place the PLA\_9 part's screw holes above the raspberry pi, so that the multiranger deck is above the rasbperry pi, then screw the PLA\_9 part into the PLA\_1 part through the raspberry pi.



8)  Screw the CW propellers with two 7mm screws each (from the motors
    package), at the front left and the back right of the drone, and the
    CCW propellers at the front right and the back left.

9)  Push the TPU\_2 parts across the wood sticks to make sure there is a
    gap of around 1cm between the propellers and the frame.

10) Solder the power cables to the FC.

**Step 9**

Last step to complete the assembly of the drone. Prepare the T265 camera.

1) Screw the PLA\_3 part into the PLA\_2 with the orientation shown in the picture below. Make sure that the screws going on the holes inside the battery slot have a head flat enough, to prevent damaging the battery.



2) Screw the T265 camera on the PLA\_4 part, so that the logo upside down, on the right side.

3) Use zip ties to attach the PLA\_4 part to the frame (on the 11cm stick). Before moving on, verify that the center of gravity of the camera is about 65mm +-15mm away from the center of the FC.



4) Put hot glue inside the zip ties, between part PLA\_4 and the frame. Proceed carefully to avoid putting hot glue on the T265. If you filp the drone to put more hot glue, turn the propellers so that they are not under the glue, otherwise it can fall on them. 

5) Use zip ties wherever you have loose cables. In particular, verify that no cable is in front of the optical flow. Trim the zip ties to avoid contact with the propellers.

**Safety precaution and troubleshooting**:  
Before connecting the battery
to the drone, it is suggested to verify with a multimeter the input and
outputs power connectors of the flight controller. If a short circuit is
detected, don’t connect the battery, and verify/redo soldering. If
verification is successful, connect the battery to the drone and make sure
flight controller is lightning up. If not, disconnect the battery
immediately and touch carefully the chip of flight controller to see if
it is overheating. If it's abnormally hot, this may indicate a short circuit
with low voltage outputs, otherwise, it could be RX/TX connections.

One extra suggestion is to wear safety glasses when operating the drone 
because the motors spin at high speeds and a faulty propeller could shatter projecting 
plastic bits towards your eyes.

The hardware of the drone is now ready. Next step will be to setup the
firmware and the configuration of the fight controller with INAV and the
files on the Raspberry Pi.

## Software setup

### INAV

The configuration of the flight controller is made with INAV. It is an
open-source firmware compatible with a wide range of flight controllers.
It allows to link the different channels to the hardware connections,
and to set the different features of the drones. The firmware developed
specifically for CogniFly requires INAV version 2.3.2, software can be
downloaded on computer
[<span class="underline">here</span>](https://github.com/iNavFlight/inav-configurator/releases/tag/2.3.2).
Setup files and general instruction can be found on
[<span class="underline">GitHub</span>](https://github.com/thecognifly/cognifly-python/blob/main/readme/DRONE_SETUP.md).

**Step 1**

Open *inav-configurator.exe* from the INAV 2.3 and go to *Firmware
flasher* tab. Connect the flight controller of the drone with a
micro-USB cable to the computer.

Une image contenant table Description générée automatiquement Une image contenant texte, capture d’écran, moniteur, plusieurs Description générée automatiquement

**Step 2**

Click on *Load Firmware \[Local\]* and select the firmware file
*cognifly\_framework.hex* which can be downloaded
[<span class="underline">here</span>](https://github.com/thecognifly/cognifly-python/releases/download/v0.0.4/cognifly_framework.hex).
Make sure full chip erase is selected. Then, click on *Flash Firmware*,
the flight controller should turn automatically in DFU mode to flash the
firmware.

Une image contenant texte Description générée automatiquement

The loading bar will first erase the content of the chip then flash it.
You should see Programming successful at the end of this process.



**Step 3**

Click on the Connect blue icon on the top right INAV window. The
connection port should automatically be detected.



**Step 4**

Go to *CLI* tab (last tab on the left menu) and click on Load from file.
Select the CLI configuration file *cognifly\_configuration.txt*, which
can be downloaded
[<span class="underline">here</span>](https://github.com/thecognifly/cognifly-python/releases/download/v0.0.4/cognifly_configuration.txt).
Click Execute on the popped-up window.



Une image contenant texte, capture d’écran, moniteur, intérieur Description générée automatiquement

**Step 5**

After execution, type *save* in the text field and press enter, flight
controller will reboot.



**Step 6**

If the flight controller doesn’t reconnect automatically, click on the
connect button. You should see a representation of the drone in the
*setup* tab. Go to the *Outputs* tab, where you will be able to test the
motors. Make sure that the propellers are free to move and applied
required safety measure (if you are not confident with the building
process, you may begin by removing the propellers of the motor shafts).
Connect the battery to the drone and enable motor control.



**Step 7**

For the initial motor tests, ***remove the propellers***, hold safely the drone and increase slowly the control
bar of motor 1. If abnormal behaviour occurs, put back control bar to 0
and solve the issue. If motor is vibrating without turning, this may be
a sign of disconnected or shorted wires (verify soldering of the three
wires). If motor turns as expected, verify the direction of rotation of
the motor. If the right propeller is on it, simply verify that air is
pushed under the drone. If wires connection has been made as in building
process, the motor should turn in the right direction (Refer to INAV
image to find motor directions). If the motor is turning in the wrong
direction, two of the three wires need to be inverted (it doesn’t matter
which ones) by resoldering them on the flight controller (Before
disordering, double check that the right propellers is on the motor
shaft).

**Step 8**

Redo step 7 with motors 2, 3 and 4.

**Step 9**

Verify that flow and sonar icons on the top of the window are blue. If
not, it may be a sign of a bad connection (verify soldering) or wrong
port. If ports of optical flow and Raspberry Pi have been changed from
building process (by purpose or not), the new ports can be selected in
the *Ports* tab.



Une image contenant table Description générée automatiquement

**Step 10**

Go to the *Calibration* tab and calibrate on a level surface the drone
by clicking on *Calibrate Accelerometer*. Follow INAV instructions.
After accelerometer calibration done, calibrate the optical flow by
clicking on *Calibrate Optical Flow sensor*, following INAV instruction.

 Une image contenant texte Description générée automatiquement

**Step 11**

Go to *setup* tab and check the hardware health and configuration with
the pre-arming checks on the right of the window. (UAV is levelled
requires the drone to be hold horizontal).



INAV configuration is now completed

### Raspberry Pi Zero 2W

The configuration of the Raspberry Pi Zero is easily made loading a disk
image on the micro-SD card. It allows to execute Python programs
controlling the drone via Wi-Fi.

**Step 12**

Download
[<span class="underline">Raspbian</span>](https://www.raspberrypi.com/software/operating-systems/)
on the SD card using *Raspberry Pi OS Lite* image. If you already have a
local disk image of a previous CogniFly, it can be used to have the Wifi
configuration set. However, the name of the new CogniFly must be
changed.

**Step 13**

A software to create disk image is required. For windows, Win32 Disk
Imager can be downloaded
[<span class="underline">here</span>](https://sourceforge.net/projects/win32diskimager/).
Insert the micro-SD card via a micro-SD to SD or micro-SD to USB adapter
so computer can access it. Open Disk imager.

Browse the image file *…-raspios-bullseye-armhf-lite.img* or your local
file *PiZeroSD.img*. Verify that the device path is pointing to the
SD-card. The process will erase the content of the SD card. Then click
on *Write* and accept erasing the SD-card.

Une image contenant texte Description générée automatiquement Une image contenant texte Description générée automatiquement

After imaging process completed, two partitions should have been created
on SD card: *boot* and *rootfs*.

**Step 14**

Access the *boot* folder of the SD card and create a file without
extension named *ssh*.

***Linux system may be required to access the rootfs partition for the
following steps!***

**Step 15**

To configure the wpa-supplicant, edit
*/rootfs/etc/wpa\_supplicant/wpa\_supplicant.conf* file. (On linux, this
may require *sudo* command), adding the following (with the name of your
wifi connection) at the end of *wpa\_supplicant.conf*. Check the [troubleshooting section](readme.md#troubleshooting)
if you need extra information.

```
network={

ssid="yourNetworkSSID"

psk="yourNetworkPassword"

scan_ssid=1

}
```

**Step 16**

Change the name of the drone. Edit the */rootfs/etc/hostname* file by
replacing the default *raspberrypi* by desired drone name. Replace also
drone name in */rootfs/etc/hosts* file.

**Step 17**

Enable the multiranger and the i2C port editing the
*/boot/config.txt* file under the *\[all\]* section, set the following
lines:
```
```dtparam=i2c_arm=on,i2c_arm_baudrate=400000```
```

**Step 18**

Disable the console messages in the serial port editing the
*/boot/cmdline.txt* file. If you see *console=serial0,115200*, remove
this command. Raspberry Configuration is done.

**Step 19**

Plug the SD card into the Raspberry Pi. Plug a charged battery or
connect the Raspberry Pi with a micro-USB cable to a computer. Wait for
the Raspberry Pi to boot, the light should stop blinking.

**Step 20**

ssh the drone from your computer with the command *ssh
pi@myDroneName.local* (the default password should be raspberry). On
Windows, if ssh is not accessible from terminal,
[<span class="underline">Putty</span>](https://www.chiark.greenend.org.uk/~sgtatham/putty/latest.html)
software can be downloaded to establish the ssh connection.

**Step 21**

When Raspberry Pi successfully connected via ssh, execute the following
on the Raspberry Pi.
```
sudo apt-get update

sudo apt-get install libatlas-base-dev libopenjp2-7 libtiff5 python3-pip
```
To use the multiranger, execute the following commands:
```
sudo apt-get install -y python-smbus i2c-tools

sudo pip install smbus2 

sudo pip install vl53l1x
```

**Step 22**

Install the cognifly-python library on the drone executing the following
command.

```
pip3 install --upgrade pip

pip3 install cognifly
```

The drone should now be ready to fly, see the section Usage on
[<span class="underline">cognifly-python
repository</span>](https://github.com/thecognifly/cognifly-python#installation)
to learn how to control the drone.

## Troubleshooting
### Wifi not working
The RPI allows the user to setup the connection by the creation of a file called ```wpa_supplicant.conf``` inside the boot partition (the only partition that will show on Windows computers when you read the SD card) and it will automatically connect in the next boot.

The beginning of the file ```wpa_supplicant.conf``` will have these lines:
```
ctrl_interface=DIR=/var/run/wpa_supplicant GROUP=netdev
update_config=1
country=<Insert 2 letter ISO 3166-1 country code here>
```
You must replace ```<Insert 2 letter ISO 3166-1 country code here>``` with your country code!

Just below the lines above, you need to use one of the patterns below according to the type of wifi network available for you (and don't forget to replace the characters between ```" "``` with your own stuff):
* ssid: wifi network name between ```" "```
* psk: wifi password between ```" "```

```
# 
# 1) Visible SSID with password
#
network={
	ssid="access_point_visible_ssid"
	psk="wifi-password"
	key_mgmt=WPA-PSK
	priority=20
	id_str="Hotspot"
}

#
# 2) Hidden SSID with password
#
network={
	ssid="access_point_hidden_ssid"
	scan_ssid=1
	psk="wifi-passpord"
	key_mgmt=WPA-PSK
	priority=10
	id_str="AP_Hidden_ssid"
}

#
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

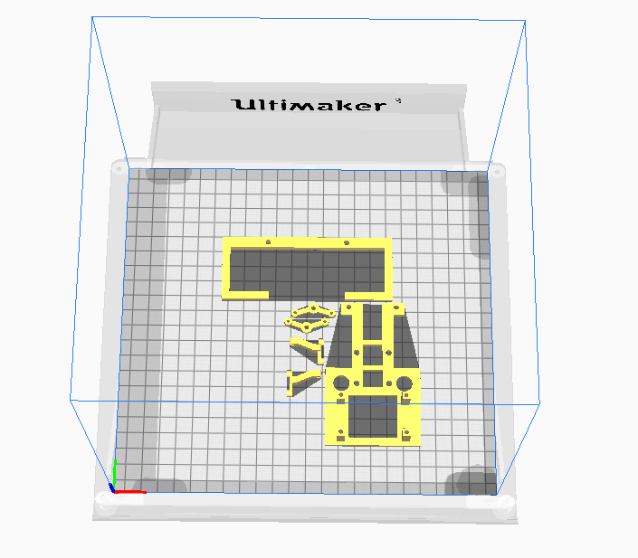
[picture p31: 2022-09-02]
Cognifly_T265/media/media/u5.PNG

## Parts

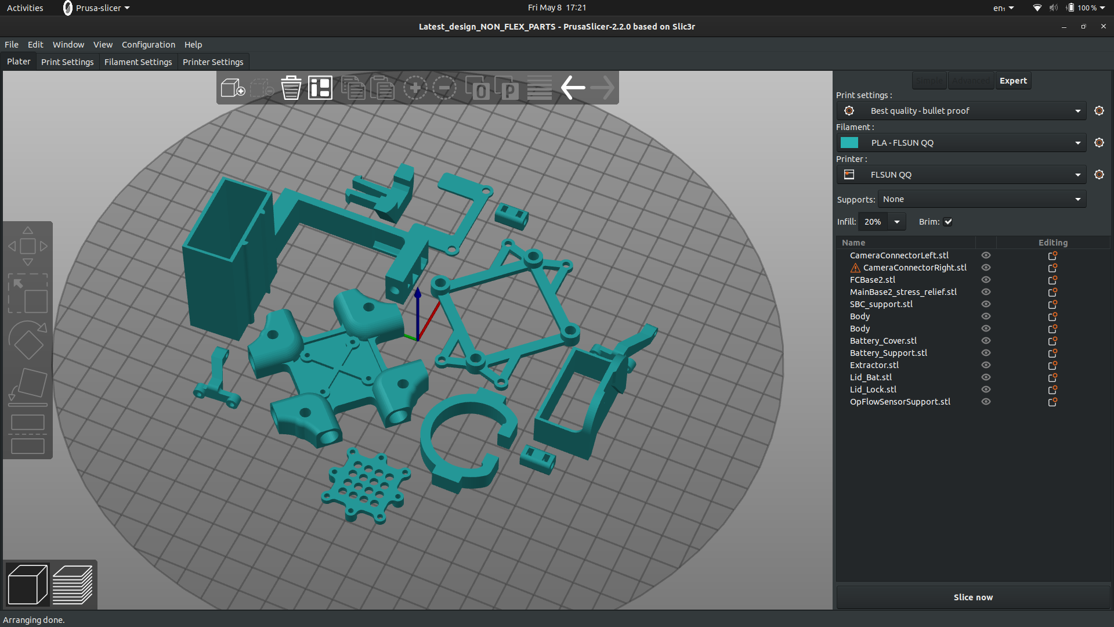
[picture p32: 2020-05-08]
CogniFly_v7/Latest_design_NON_FLEX_PARTS.png

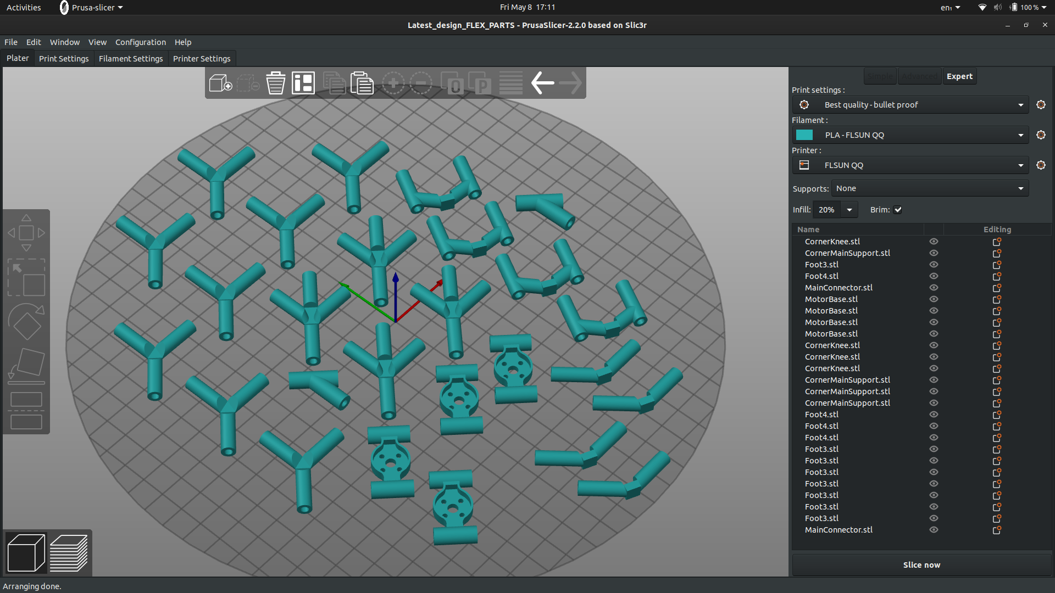
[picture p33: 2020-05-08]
CogniFly_v7/Latest_design_FLEX_PARTS.png

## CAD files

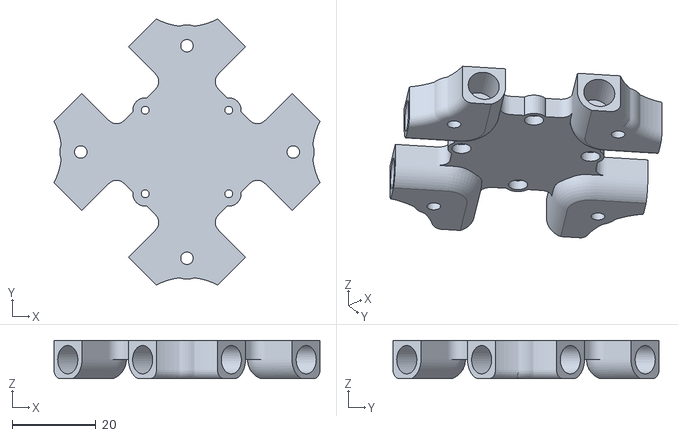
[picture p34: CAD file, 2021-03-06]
Rigid_Curved_Legs/MainBase.stl
63.6 x 63.6 x 9.10

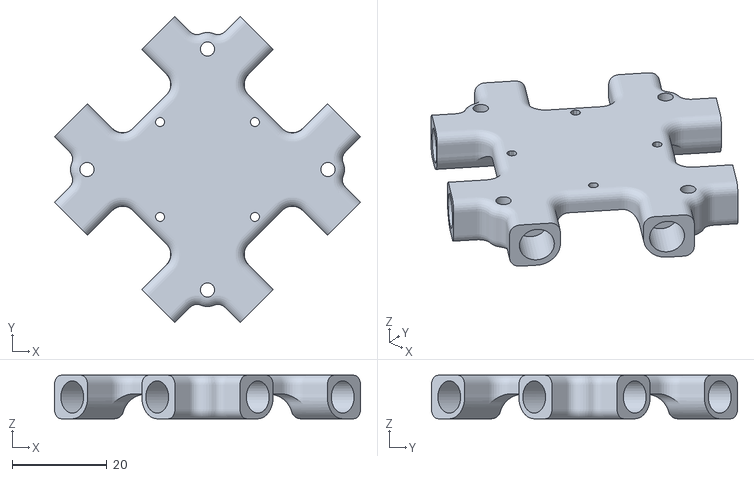
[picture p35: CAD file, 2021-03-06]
CogniFly_v8_Crash_Tests/MainBase.stl
64.5 x 64.5 x 9.20

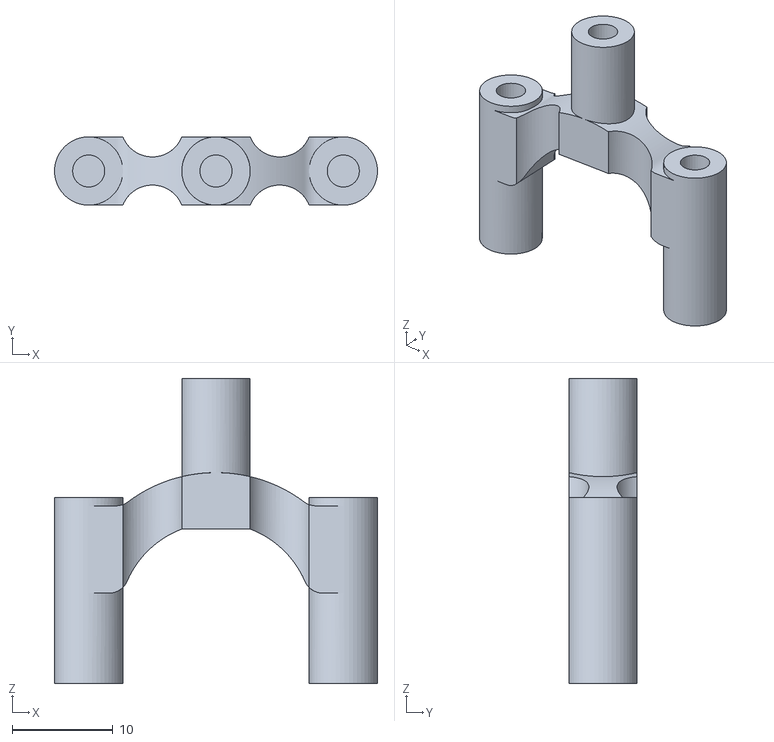
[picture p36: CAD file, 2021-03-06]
Cognifly_T265/TPU/Flex_Main_connector_new_bumper.stl
32.1 x 6.80 x 30.4

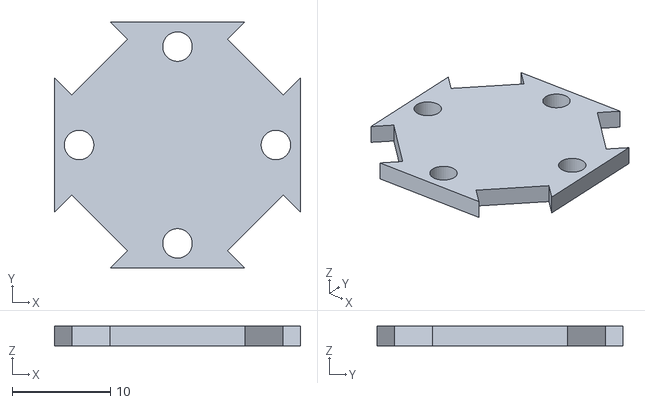
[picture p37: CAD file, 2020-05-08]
NeverBuilt/MainBase.stl
25.0 x 25.0 x 2.00

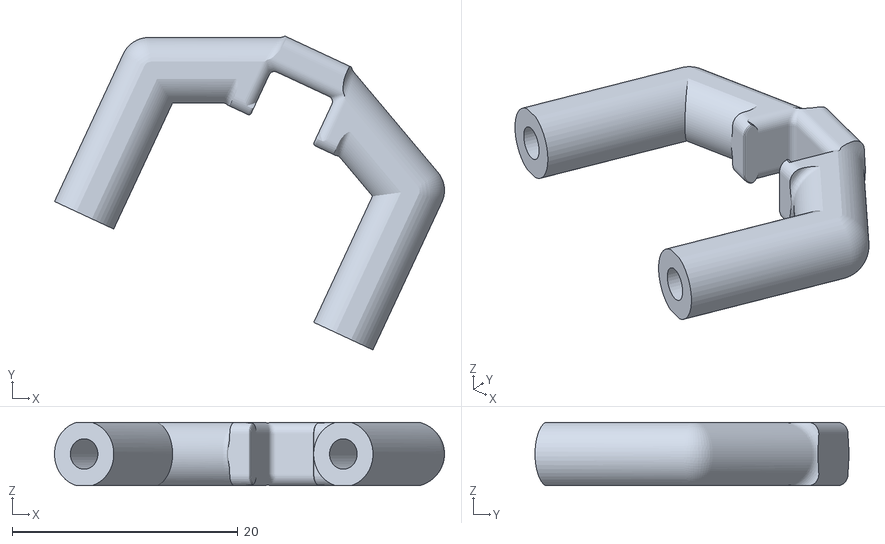
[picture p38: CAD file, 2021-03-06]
Cognifly_T265/TPU/Flex_CornerMainSupport_updated.stl
34.5 x 27.8 x 5.60

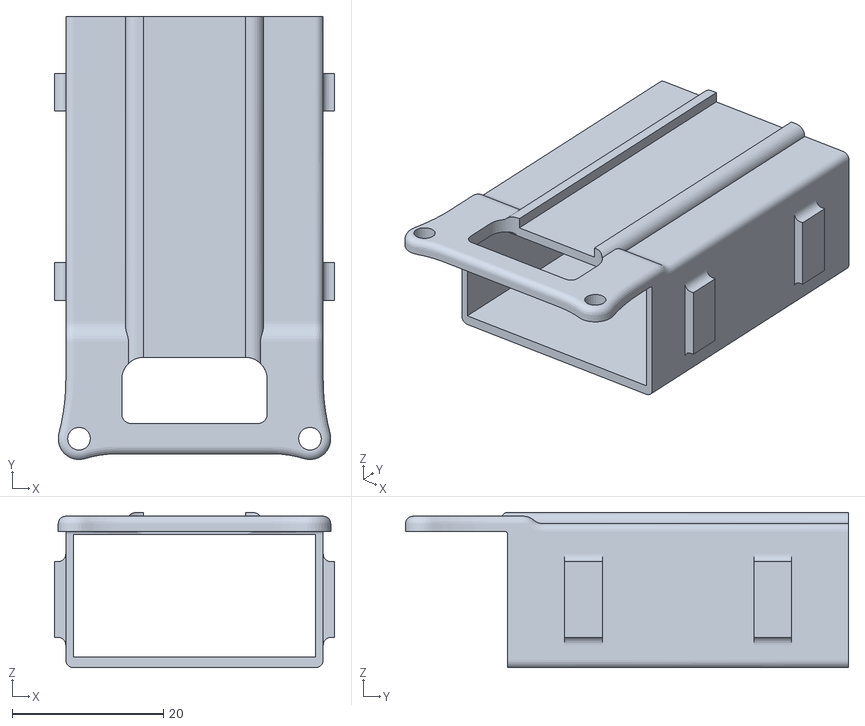
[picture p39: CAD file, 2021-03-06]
CogniFly_v8_Crash_Tests/Battery_holder_magnetic_main.stl
37.0 x 58.5 x 20.5

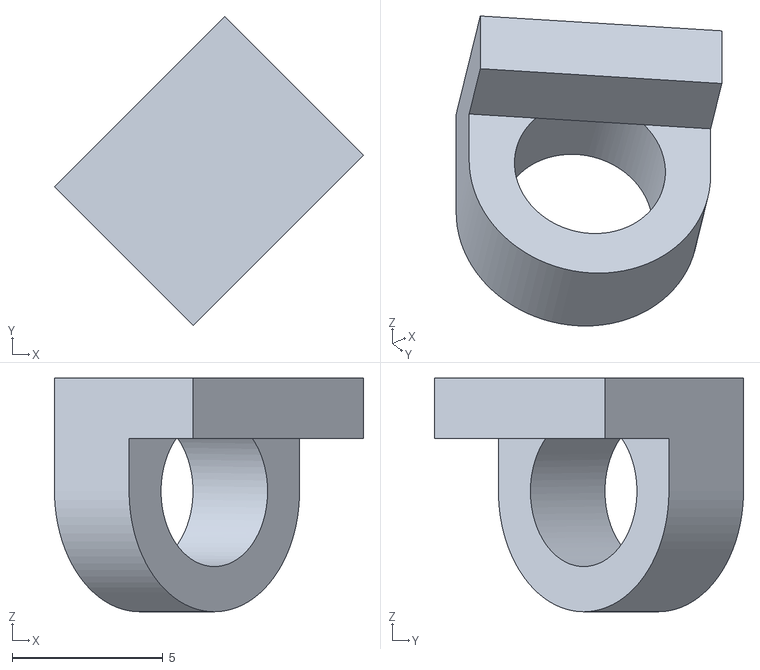
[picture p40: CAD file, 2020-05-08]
NeverBuilt/MainBaseConn.stl
10.3 x 10.3 x 7.75

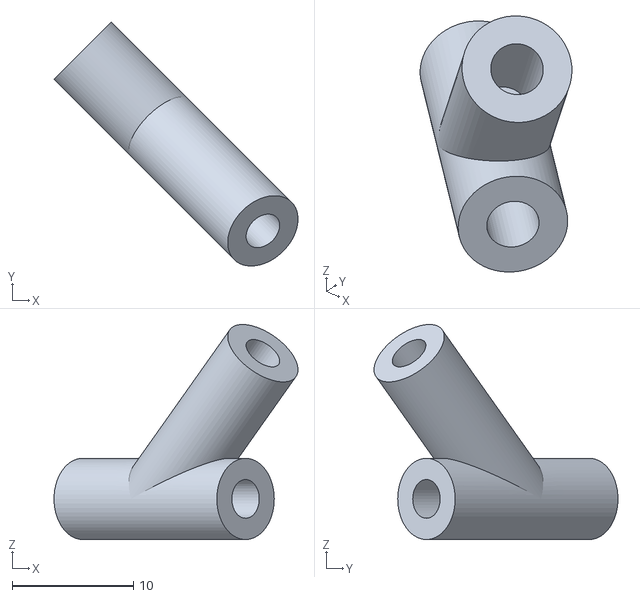
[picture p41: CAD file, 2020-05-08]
CogniFly_v7/MainConnector.stl
20.1 x 20.1 x 17.7

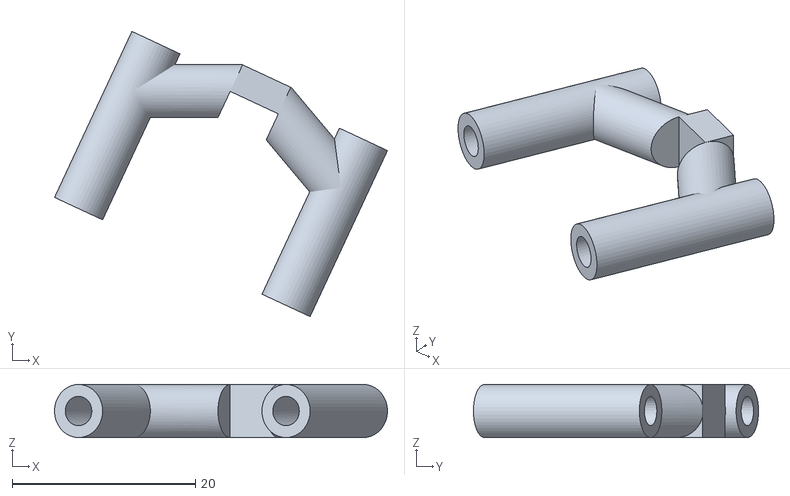
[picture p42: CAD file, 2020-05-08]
CogniFly_v7/CornerMainSupport.stl
36.4 x 31.1 x 5.80

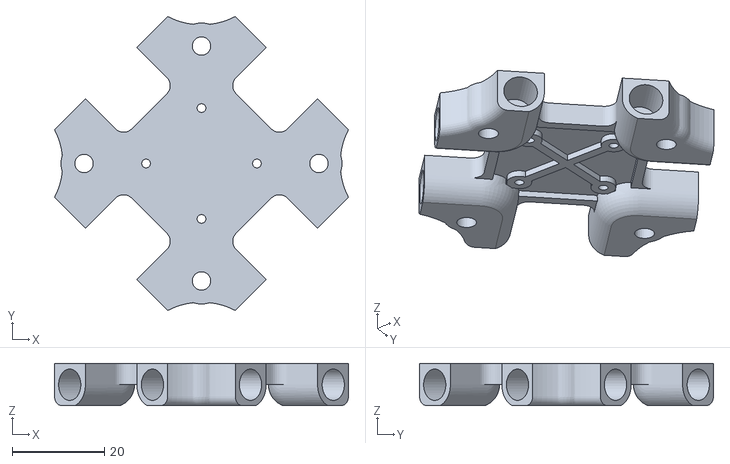
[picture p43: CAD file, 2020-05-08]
CogniFly_v7/MainBase2_stress_relief.stl
63.6 x 63.6 x 9.10

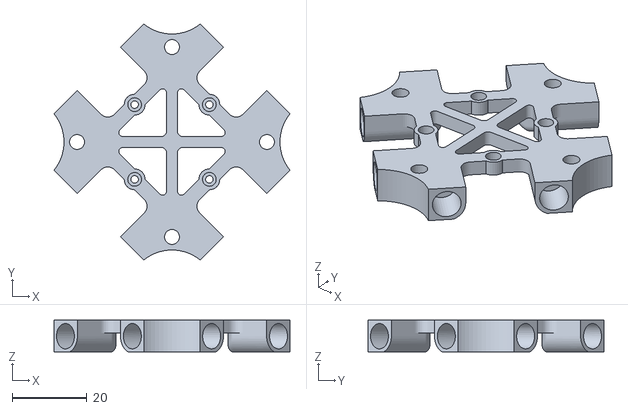
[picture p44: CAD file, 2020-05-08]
CogniFly_v7/MainBase2_stress_relief_NEW_HOLE.stl
63.2 x 63.2 x 8.50

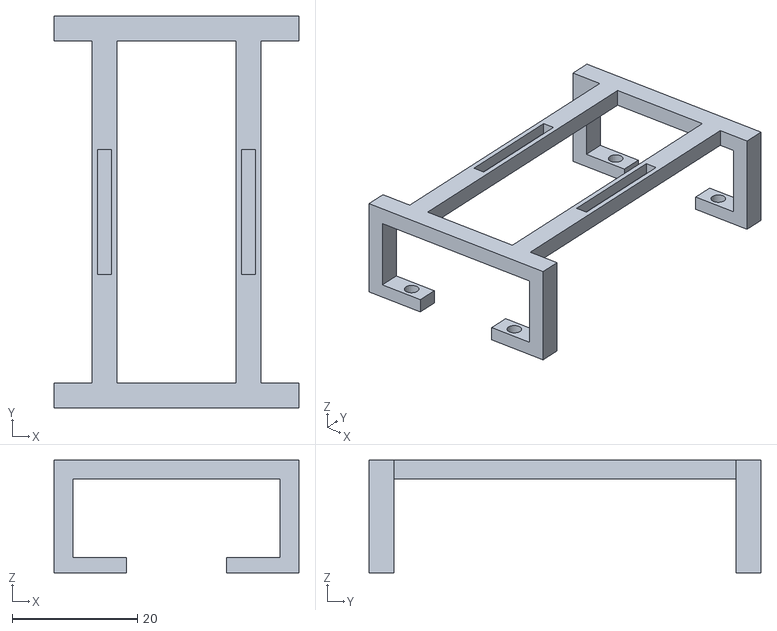
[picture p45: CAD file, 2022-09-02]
Cognifly_T265/PLA/multirangerMount.stl
39.0 x 62.5 x 18.0

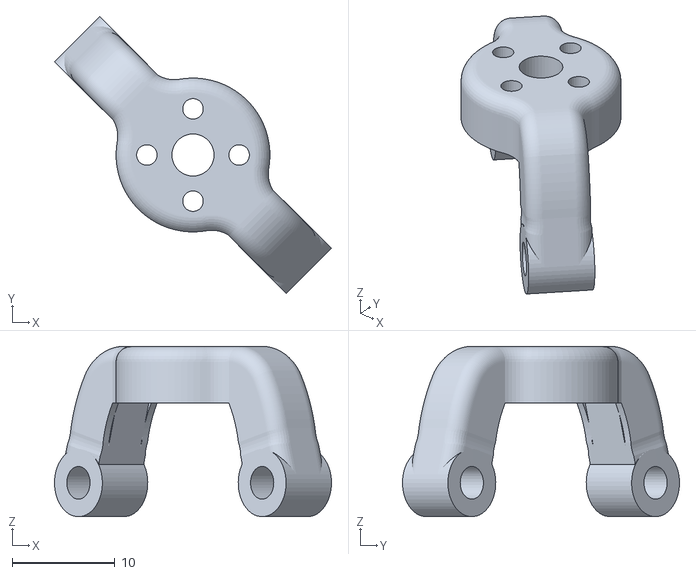
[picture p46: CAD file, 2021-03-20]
Cognifly_T265/TPU/MotorBase_Shorter_Tallest.stl
27.0 x 27.0 x 16.6

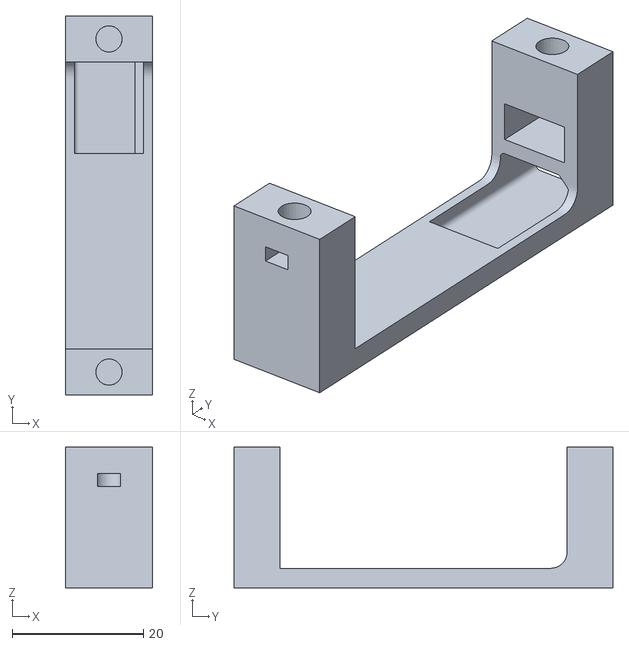
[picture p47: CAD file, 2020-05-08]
CogniFly_v7/BatteryHolder/Battery_Support.stl
13.2 x 57.8 x 21.5

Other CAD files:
CogniFly_v8_Crash_Tests/STEP_and_SAT/MainBase.stp
CogniFly_v8_Crash_Tests/STEP_and_SAT/Battery_holder_magnetic_main.stp
CogniFly_v8_Crash_Tests/STEP_and_SAT/Main_connector_new_bumper.stp
CogniFly_v8_Crash_Tests/STEP_and_SAT/CornerMainSupport_updated.stp
CogniFly_v0/Base v17.step
CogniFly_v0/Body11.stl
CogniFly_v1/Arm.stl
CogniFly_v1/Battery_Holder.stl
CogniFly_v1/Leg_all-in-one_left.stl
CogniFly_v1/Leg_all-in-one_left_back.stl
CogniFly_v1/Leg_all-in-one_right.stl
CogniFly_v1/Leg_all-in-one_right_back.stl
CogniFly_v1/Main_Body.stl
CogniFly_v1/New New Frame v87.step
CogniFly_v1/Propeller_Guard.stl
CogniFly_v2/Battery_Connector.stl
CogniFly_v2/Battery_holder_xt60.stl
CogniFly_v2/Leg.stl
CogniFly_v2/Main.stl
CogniFly_v2/MonoBlockFrame v99.step
CogniFly_v2/Propeller Guard Individual v7.step
CogniFly_v2/Propeller_Guard.stl
CogniFly_v2/RPI_CAM_Connector.stl
CogniFly_v2/RPI_LEG_LEFT.stl
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

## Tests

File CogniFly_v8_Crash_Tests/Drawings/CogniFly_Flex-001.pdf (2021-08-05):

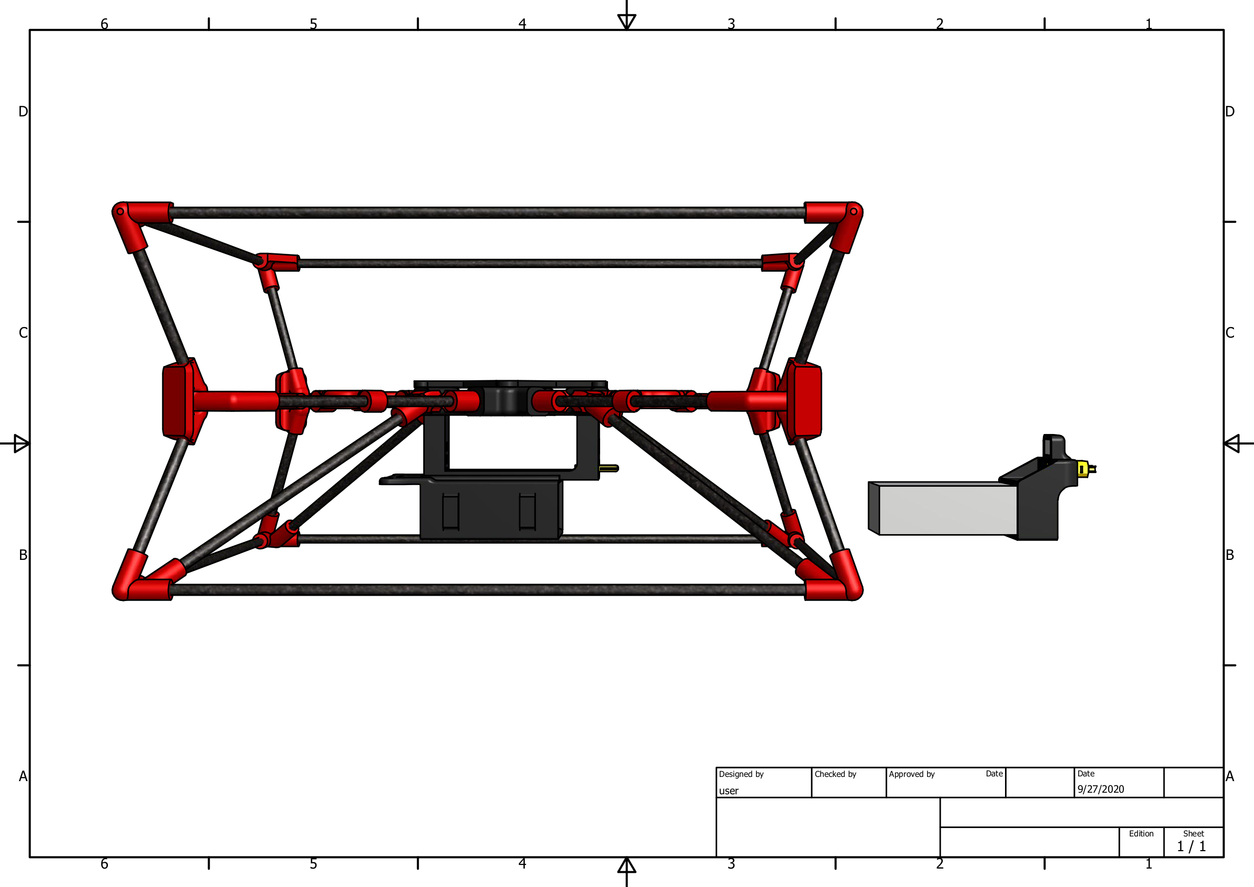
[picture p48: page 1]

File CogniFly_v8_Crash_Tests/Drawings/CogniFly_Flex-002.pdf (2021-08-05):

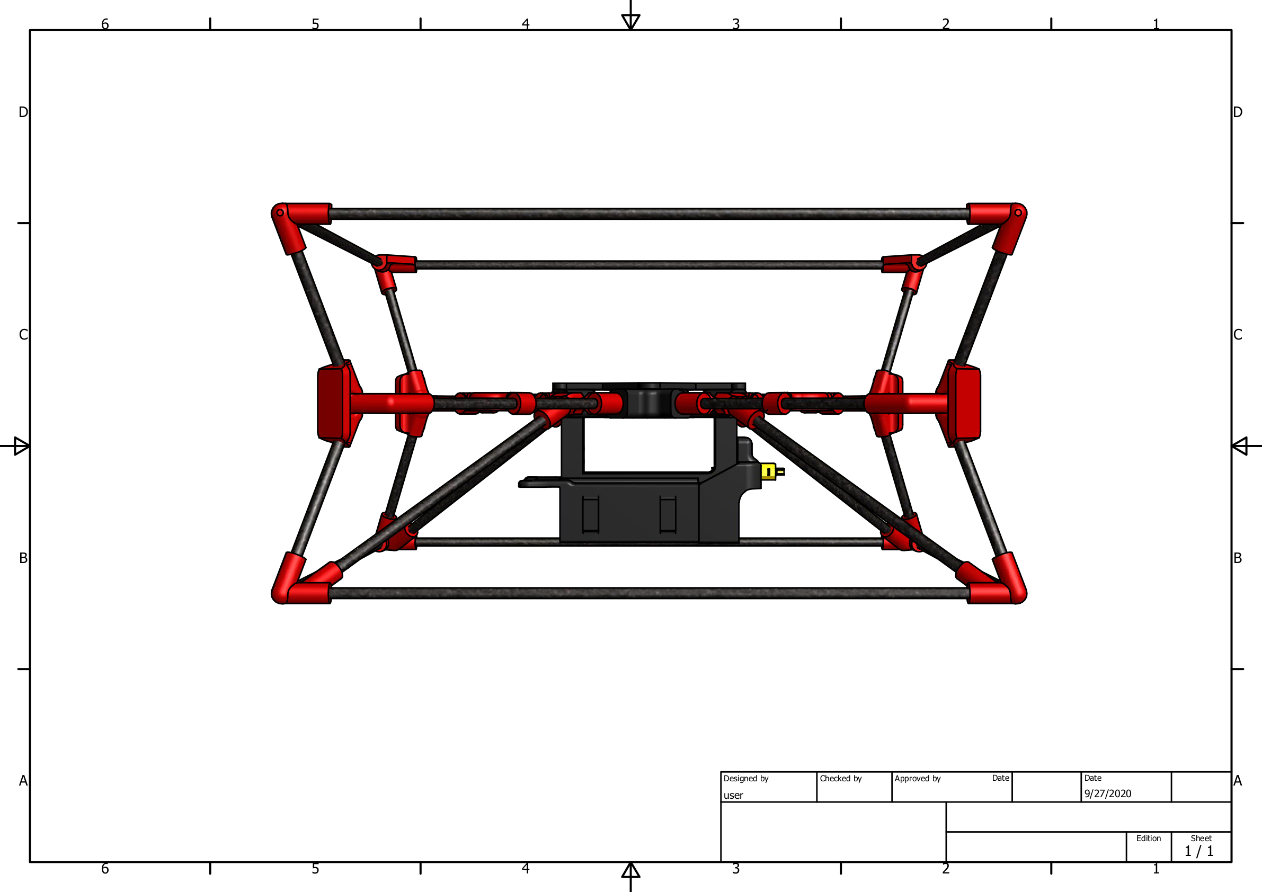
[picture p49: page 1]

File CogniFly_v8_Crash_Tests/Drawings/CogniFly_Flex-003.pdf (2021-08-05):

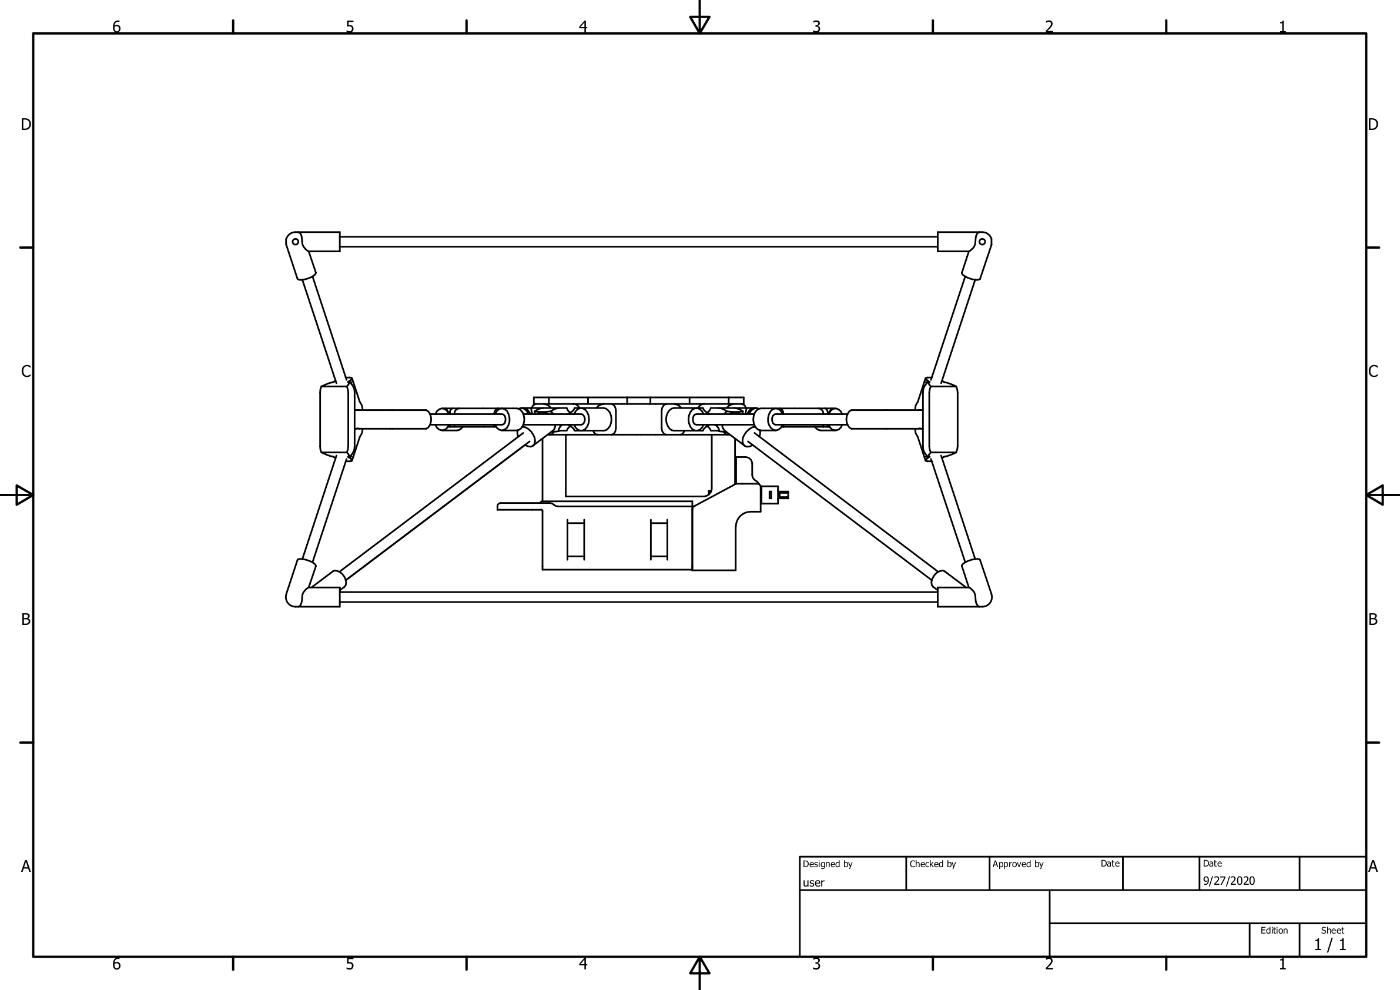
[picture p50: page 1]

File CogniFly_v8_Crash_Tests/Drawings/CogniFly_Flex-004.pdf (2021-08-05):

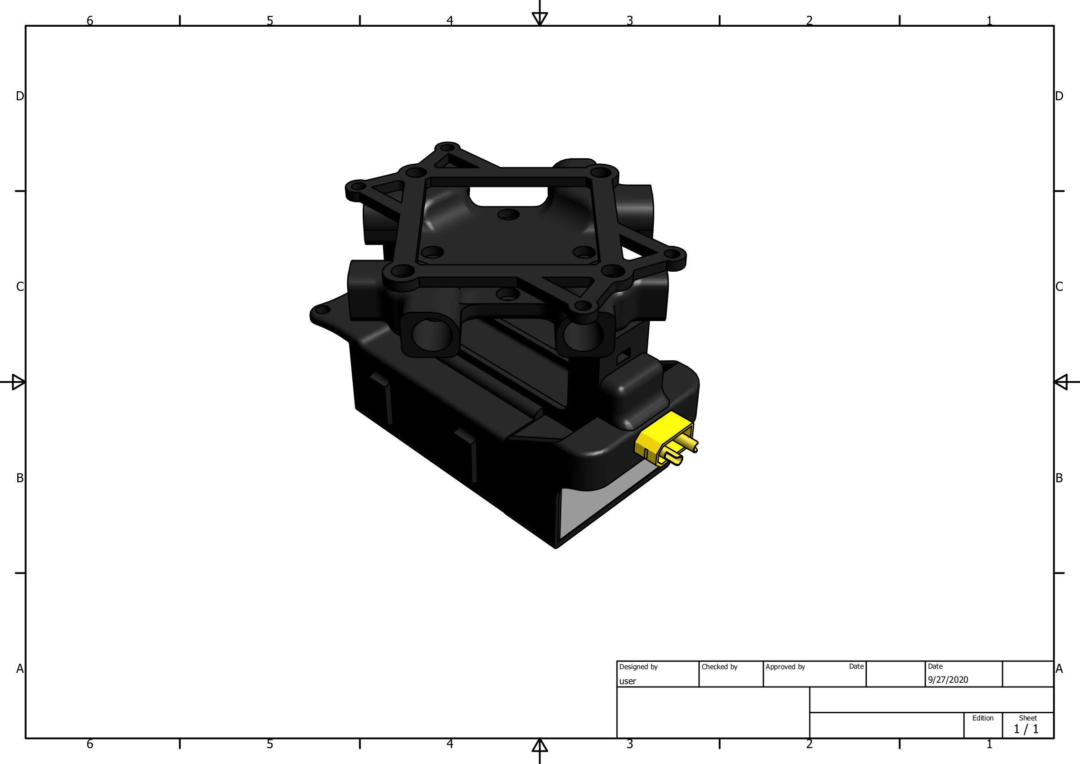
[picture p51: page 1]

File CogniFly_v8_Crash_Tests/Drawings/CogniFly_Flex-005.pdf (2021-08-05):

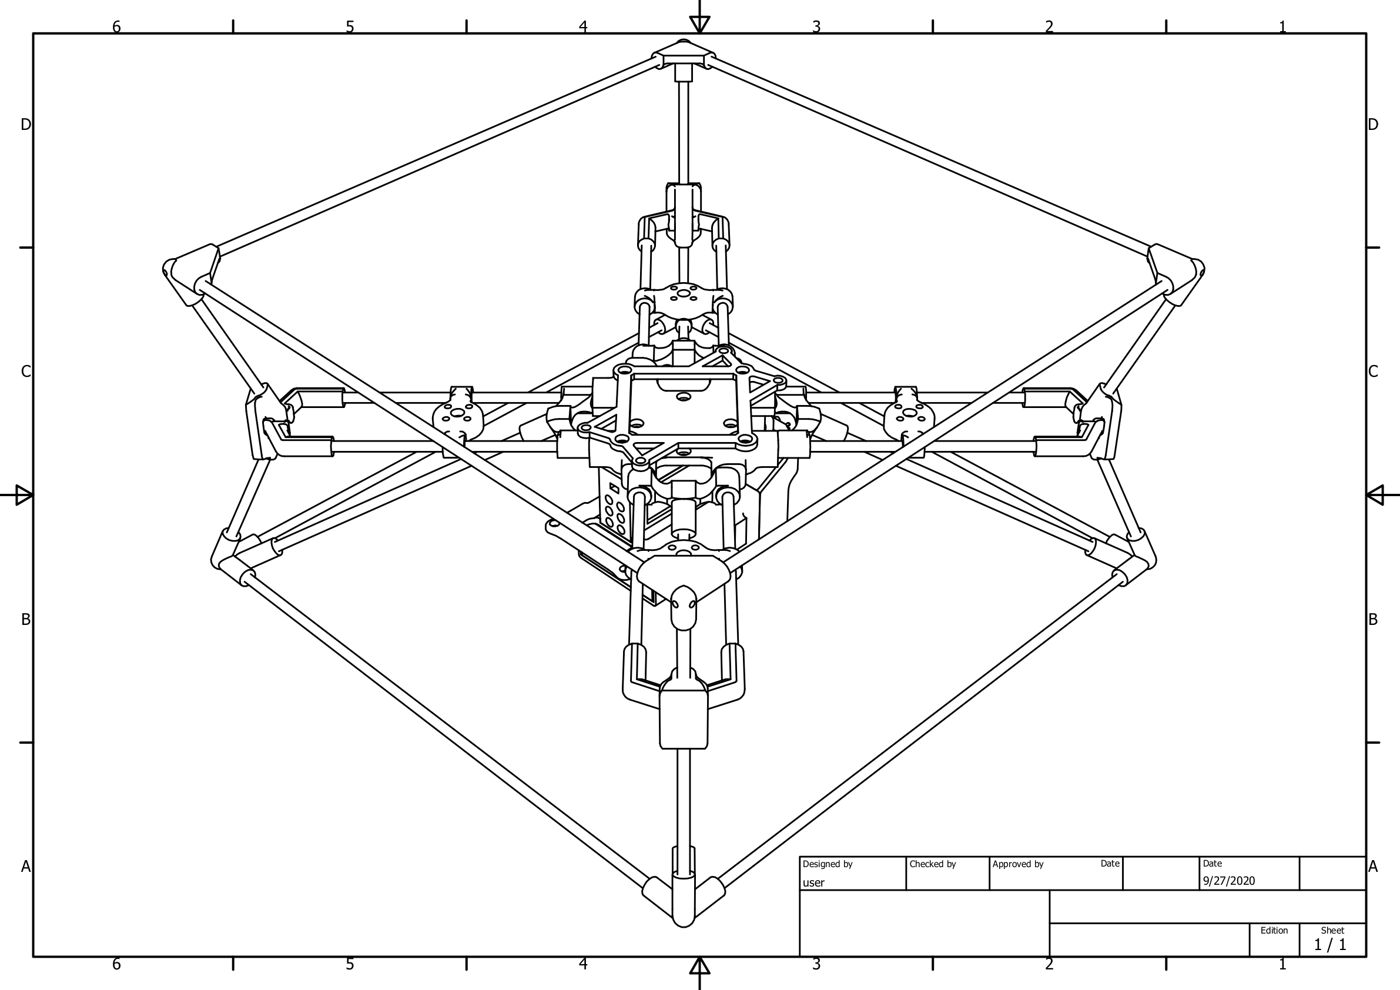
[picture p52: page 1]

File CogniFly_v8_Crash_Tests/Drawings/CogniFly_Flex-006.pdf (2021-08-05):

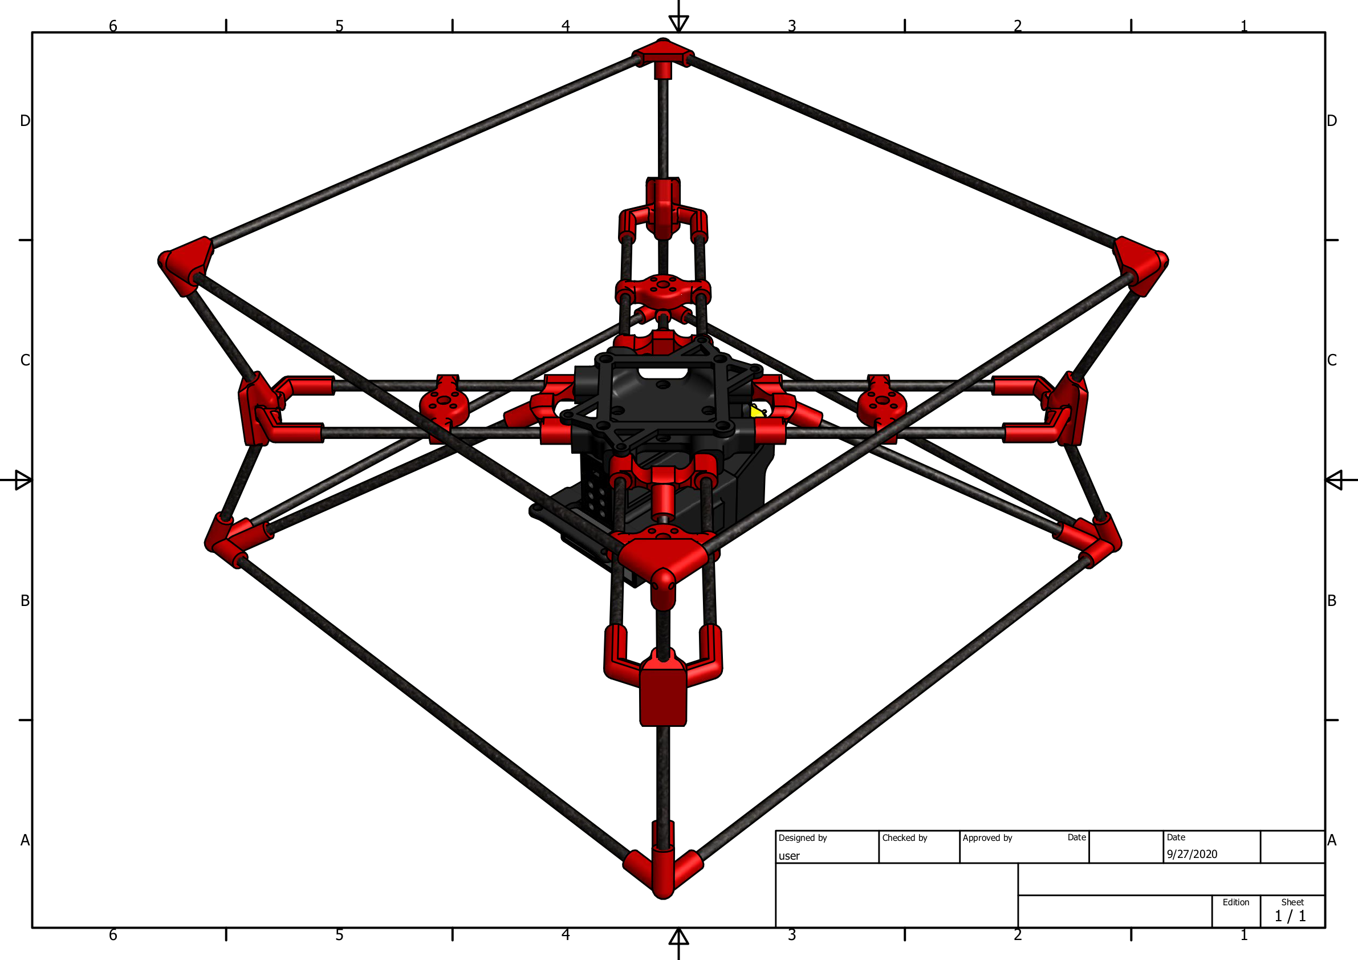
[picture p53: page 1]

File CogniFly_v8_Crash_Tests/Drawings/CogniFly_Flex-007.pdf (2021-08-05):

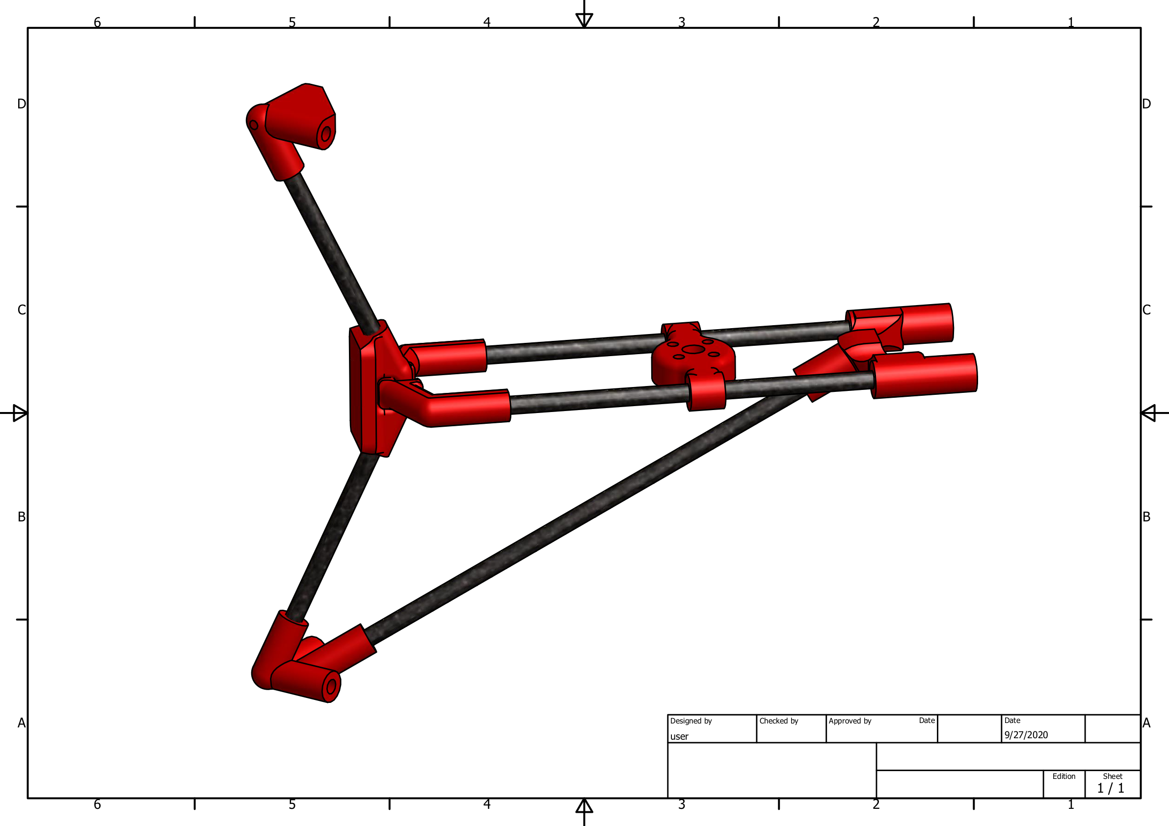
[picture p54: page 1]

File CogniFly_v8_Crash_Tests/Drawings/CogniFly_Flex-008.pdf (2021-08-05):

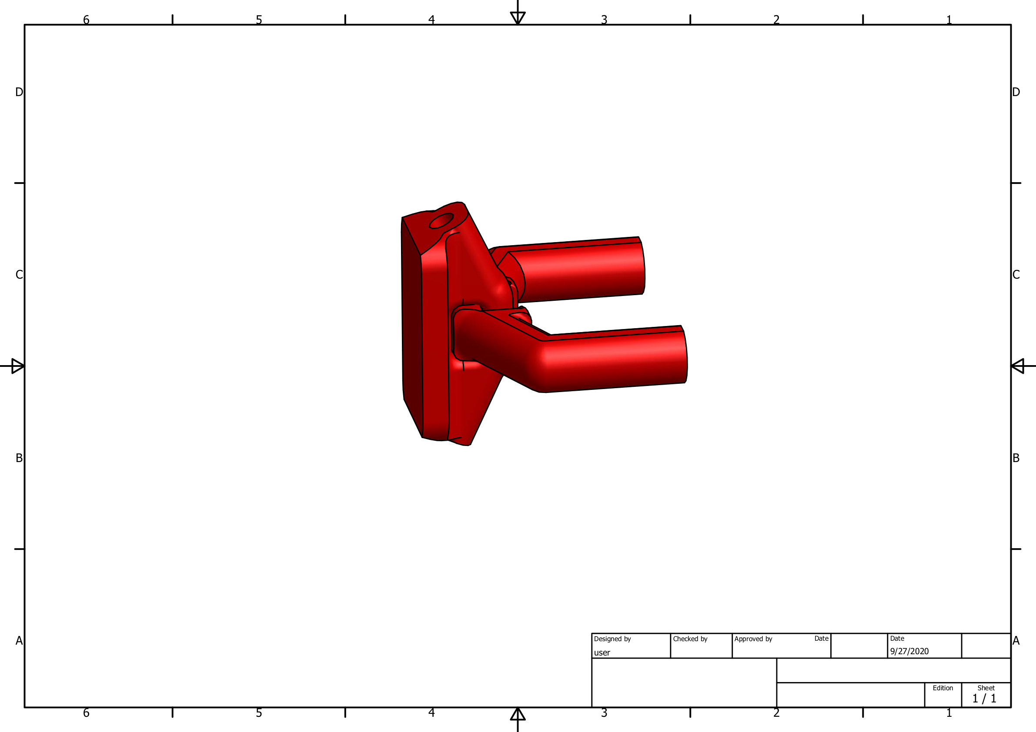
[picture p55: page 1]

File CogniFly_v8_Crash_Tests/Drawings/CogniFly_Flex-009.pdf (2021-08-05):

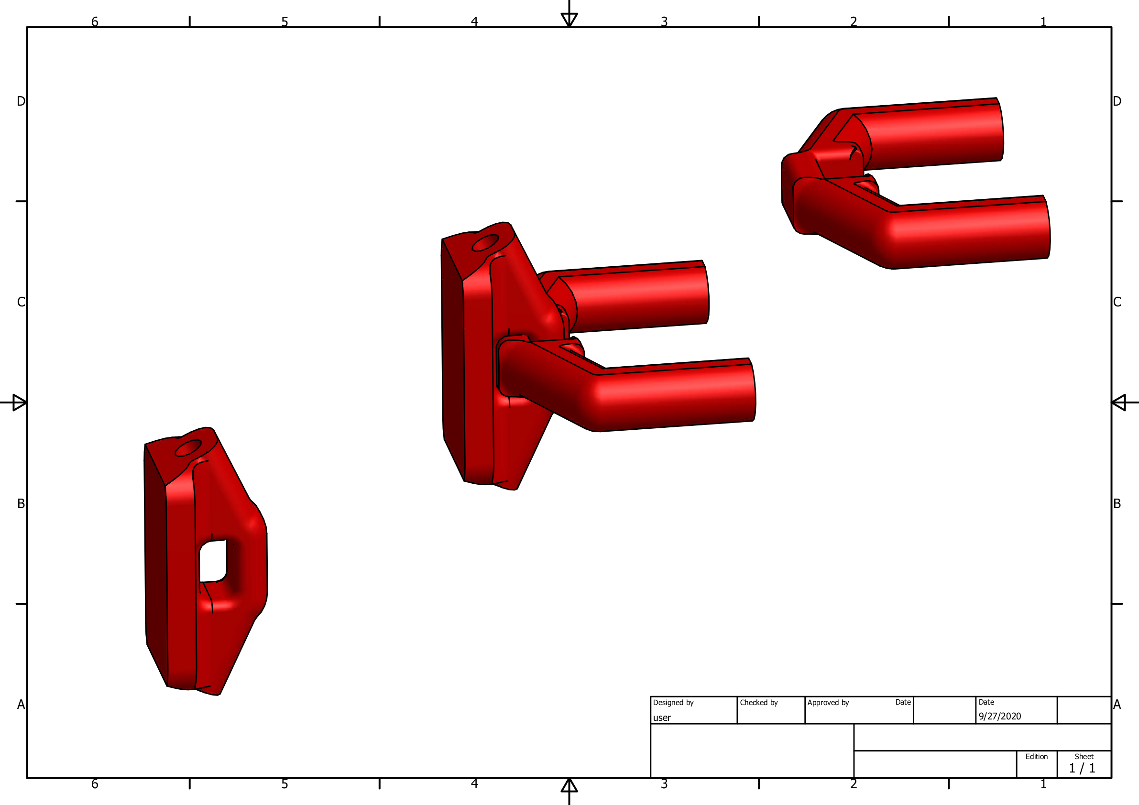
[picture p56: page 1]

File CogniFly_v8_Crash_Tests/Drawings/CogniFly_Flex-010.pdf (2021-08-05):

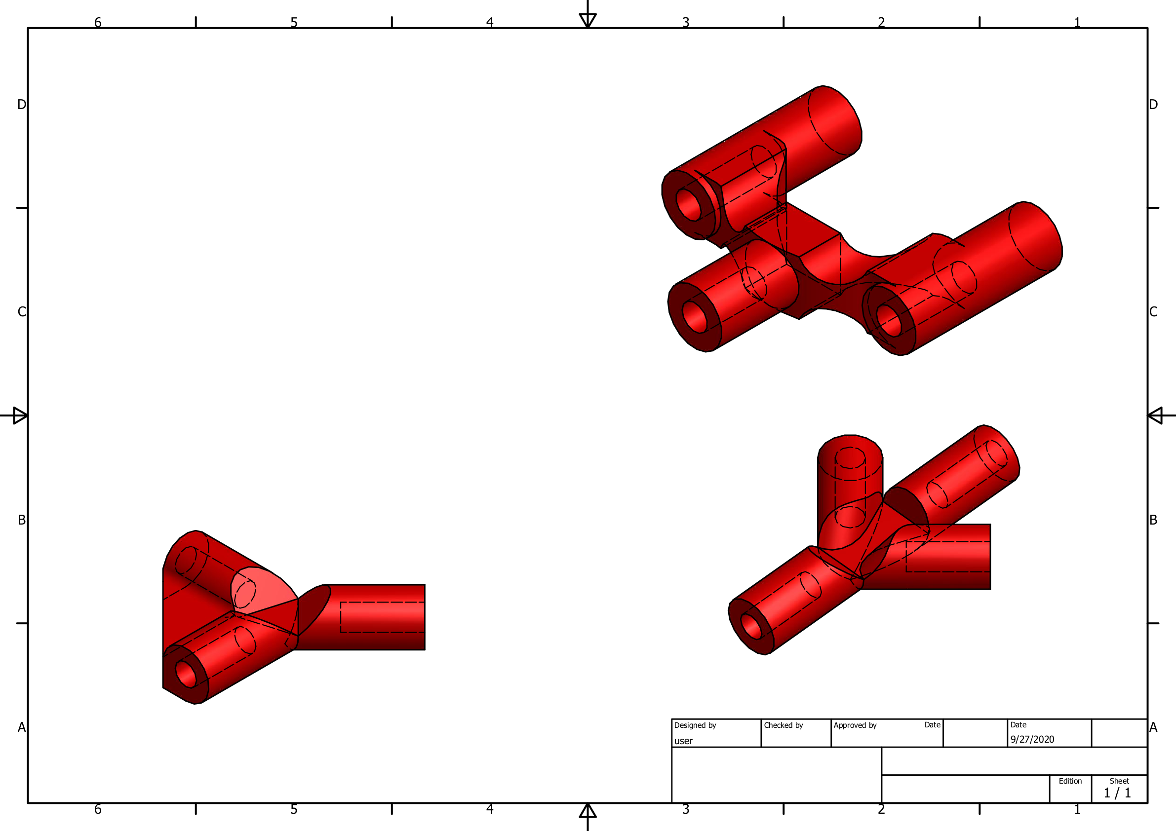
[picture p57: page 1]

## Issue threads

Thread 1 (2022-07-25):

Support for Google Coral Mini Dev Board

nicolasj92, 2022-07-25:
Hi, it is mentioned that the Google Coral Mini Dev Board is supported.
Is there any information available on how to use it? Its hardware layout is different to the RPI Zero and most likely other 3D printed parts are needed.

ricardodeazambuja, 2022-08-03:
Hi. The Coral Dev Board Mini is very much a WIP, but I suppose we will be releasing some STL files later on this year (if you are in a hurry, you can just design a simple adapter from the RPI Zero holes to the Coral Dev Mini). Remember to use the ttyS1 to connect the Coral Dev Board Mini to the flight controller.

nicolasj92, 2022-08-04:
Ok, I will try to make it work and then possibly contribute to the instructions

yannbouteiller, 2025-07-04:
Hi @ricardodeazambuja , the coral support files are here: https://git.mistlab.ca/oduguay/Coral_Cognifly/-/tree/master/Coral_support?ref_type=heads , we should merge with this repo?

ricardodeazambuja, 2025-07-04:
Hi @yannbouteiller. Yes, I agree with you.  it would be useful to have it here together with the other versions. Maybe we should also talk to David's lab people to copy their modifications here too.

yannbouteiller, 2025-07-05:
I don't know about David since their modifications consist of sticking a CrazyFlie base on top of the Cogni to get UWB, it sounds a bit niche, but the Coral Dev Board design is a small variation of the Pi Zero design. It is very useful as it has a TPU and supports 5G wifi, the only problem is that Coral boards do not like to be hot-unplugged and thus can get bricked if not handled with extra care.

ricardodeazambuja, 2025-07-05:
Ideally it would need a way to detect the battery is running low. The problem is only battery voltage won't tell you that because the voltage oscillates quite a bit depending on the current drain to the motors. It would need something running in the background, sampling the voltage and making a decision based on more than just one sample.
This could be an option: INA219 I2C Bi-Directional DC Current Power Supply Sensor Breakout Module

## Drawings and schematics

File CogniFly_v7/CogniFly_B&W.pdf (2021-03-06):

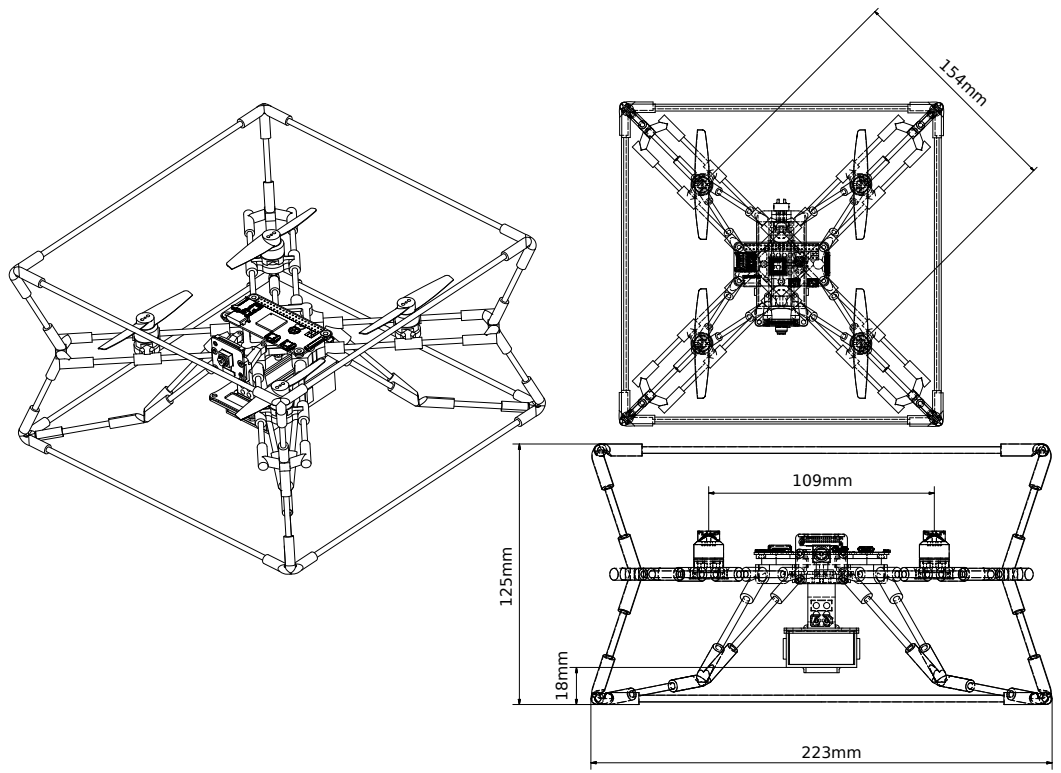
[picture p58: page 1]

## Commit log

2020-05-08 First commit, old versions
    [Arm.stl, Bamboo1.stl, Bamboo2.stl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]
2020-05-08 Images showing how the parts should be printed
2020-05-08 Latest version
    [Battery_Cover.stl, Battery_Cover_with_sensor_support.stl, Battery_Support.stl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]
2020-05-08 Battery support changed printing orientation
    [Latest_design_NON_FLEX_PARTS.zip.amf]
2021-03-06 updated with arxiv paper version
    [Battery_Cover.stl, Battery_Cover_with_sensor_support.stl, Battery_Support.stl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]
2021-03-06 experimental all 3D printed rigid, curved legs
    [Battery_holder_magnetic_lid.stl, Battery_holder_magnetic_main.stl, Battery_holder_magnetic_support.stl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]
2021-03-14 Added the parts as they should be laid on the printer bed
2021-03-14 3D CAD, easier to modify than STL
    [Battery_holder_magnetic_lid.stp, Battery_holder_magnetic_main.stp, Battery_holder_magnetic_support.stp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]
2021-03-14 How to assemble the corners
2021-03-20 experimental motor bases
    [MotorBase_Shorter_Taller.stl, MotorBase_Shorter_Tallest.stl]
2021-03-20 Added BOM
2021-07-22 Update about the UART connection
    ST32 uC uses 3.3V, so its pins follow that same pattern unless there is an external circuit modifying that
2021-07-22 Removed info about level shifter
    It seems most FCs are 3.3V
2021-10-29 update with RA-L submission
    [Battery_holder_magnetic_lid.stl, Battery_holder_magnetic_lid.stp, Battery_holder_magnetic_main.stl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]
2021-12-16 Clarification about the weight and screws, etc
2021-12-20 Add info about screws damaging coils
2021-12-20 Files from @CharlesSol7
    Files created during @CharlesSol7 internship
    [LiIon holder - Blossom 1048 modified.stl]
2021-12-20 Add files via upload
    Files created / modified during @CharlesSol7 internship.
    [BatteryCap.stl, BatteryHolder.stl, BatteryHolderSupport.stl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]
2022-08-26 Modified readme, added stl files and f3d files
    [Camera_Connector_L - Camera_Connector_L.stl, Camera_Connector_R - Camera_Connector_R.stl, Flex_CornerKnee_updated.stl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]
